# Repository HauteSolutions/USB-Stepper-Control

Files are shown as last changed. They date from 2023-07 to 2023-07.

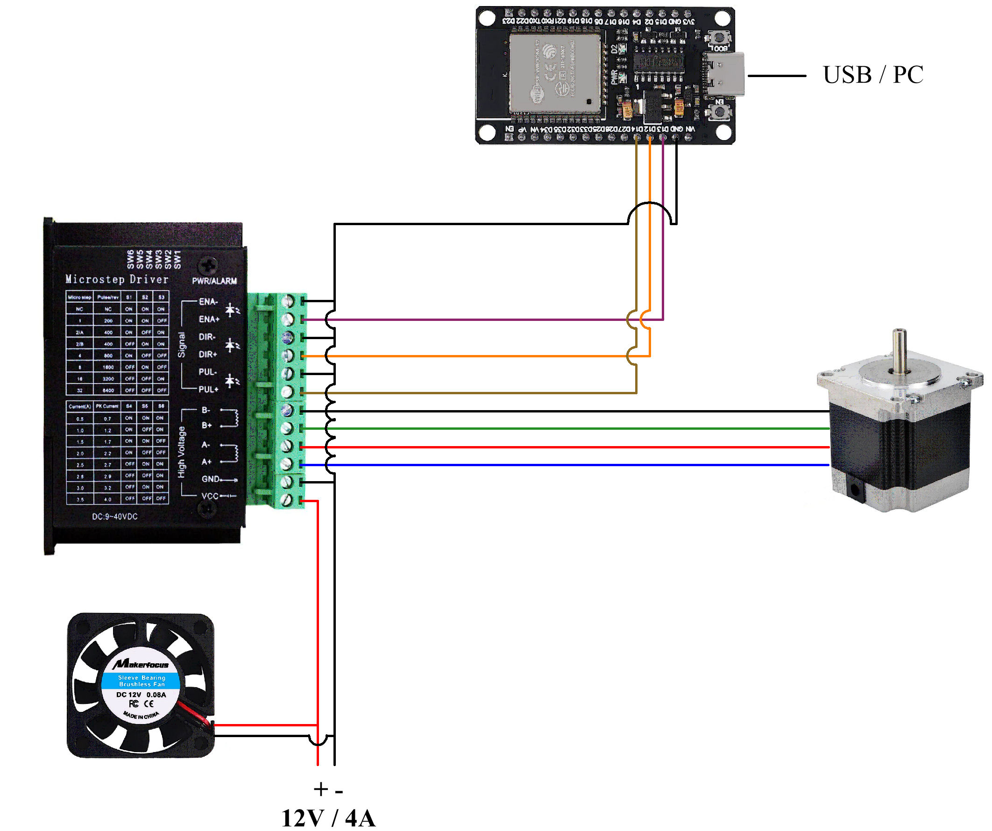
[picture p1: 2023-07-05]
Controller_Schematic.jpg

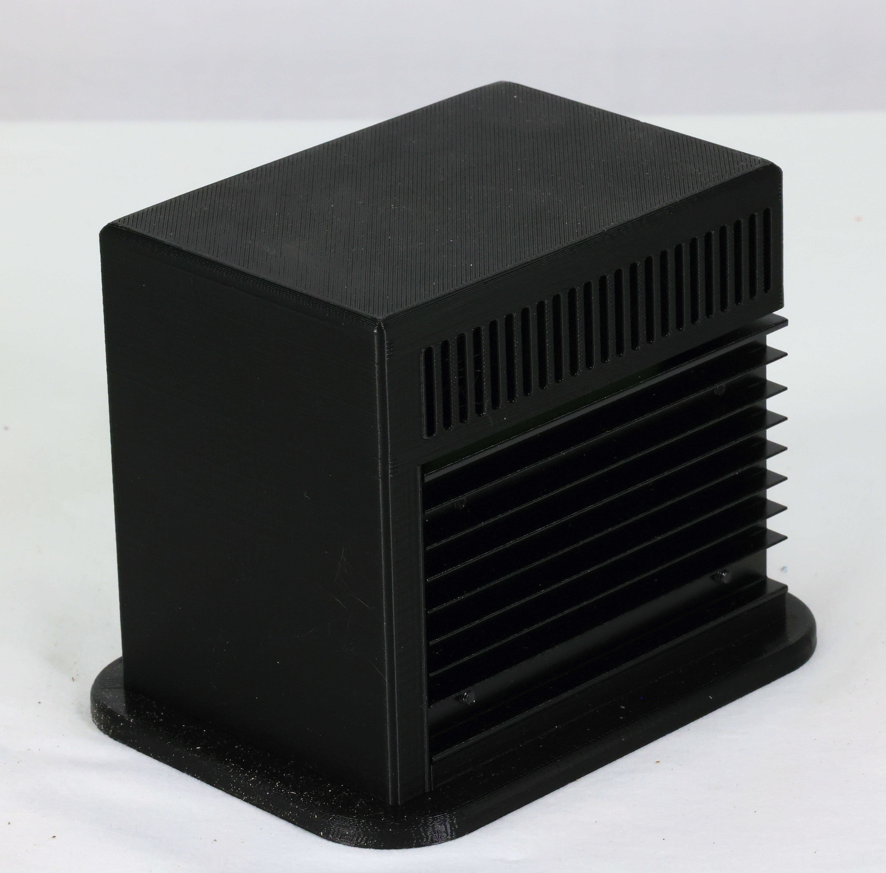
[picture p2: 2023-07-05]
photos/Controller Front.jpg

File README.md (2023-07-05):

# USB-Stepper-Control (and Rotary Pen Table Project)

A set of tools to provide simple control of a stepper from a PC USB Interface (Bridge: PC USB to AccelStepper Arduino Library)

The USB Stepper Control project provides direct control of stepper motors via a USB Connection to a PC.  This enables extended functionality for devices to be controlled via user interfaces or events directly from a Windows PC.  This project also includes the necessary 3D print files, parts list, and wiring diagrams to create a fully functional Rotary Pen Table for laser etching pens.  (The Rotary Table was the driving goal for this project!)

The Physical Connections are as follows:

     PC USB Serial Connection -> Microcontroller (ESP32, Arduino, etc) -> Stepper Driver -> Stepper Motor

The Logical Functionality is as follows:

     PC Interface (AutoIT) -> Microcontroller Control Software (ESP32, Arduino, etc) -> AccelStepper Arduino Library

There are two parts to this project:

1.  Microcontoller Side:  The microcontroller side utilizes the popular "AccelStepper" library to control a stepper driver/motor.  The AccelStepper library functions are effectively abstracted over a USB Serial interface.  A serial handshaking protocol is used to pass commands to the microcontroller (Arduino, ESP32, etc).  Both blocking and non-blocking functions are supported.  Basically, all "AccelStepper" functions are implemented and supported by passing serial commands directly over the usb interface with the appropriate number of parameters.  The Microcontroller side is simply used to objectify the library and once uploaded, very little ongoing maintenance should be required in order to maintain the microcontroller side as projects are added or updated on the PC Side.  (IOW: Functional logic can be entirely implemented/maintained on the PC side)  The microcontroller side should be largely static unless changes are required to support additional updates to the AccelStepper Library.

* Note that the Microcontroller (Arduino/ESP32) Side requires the AccelStepper Library: https://www.airspayce.com/mikem/arduino/AccelStepper/

2.  PC Side: The PC side exposes the "AccelStepper" function calls over the USB Serial Interface.  The actual function call is implemented as the first field in the serial command with additional fields provided for each of the required function parameters.  This effectively allows AccelStepper library functions to be directly called from a PC Application.

* Note that the PC (Autoit Side) requires the "ComUDF" Function Library:  https://www.autoitscript.com/forum/topic/189190-serial-port-udf-com-port-udf/

Once the Microcontroller code (USBStepperCtl.ino)is compiled and uploaded (to Arduino, ESP32, etc) then the PC Side (AutoIT) can be used to control the associated stepper.  Example code is provided using the AutoIT development environment (free).  (AutoIT excels in the simplicity of user interface creation, scripts can be compiled into standalone executables, and the development environment is freely available). The following example code fully implements the command construction and handshaking as required to implement the associated protocol.

PC (AutoIT) Examples:

USBStepperCtl.au3:  This is a very simply script demonstrating three different ways to move a stepper between various positions.  The associated INI file (of the same name) can be used to configure the operation of the program.  The [Config] section is used to define the COM Port where the stepper controller is connected, which demo program is to be run (RunDemo=Demo1, Demo2, or Demo3).  It also supports the ability to specify/maintain specific configuration parameters within separate INI sections (RunConfig=).  "MinPulseWidth" is also supported which is reportedly required for TB6600 Stepper Drivers.  The USBStepperCtl example provides no user interface and will simply run until the process is manually terminated.

Indexer.au3:  Is a sample utility developed to drive a rotary "Pen Table" for engaving using a Galvo Laser.  The format of the INI file is much like that used for USBStepperCtl example (above).The "RunConfig" option is used to designate a section which defines the stepper driver configuration parameters.  The Indexer example user interface supports initial adjustment/alignment of the rotary table (Tweak), an indexing function, the ability to disable/enable the stepper motor (for manual rotation or power savings), and a QUIT function.  Additionally, The Indexer utility (once compiled) can be called directly from the command line to control the rotary table using the command line parameters of "CW" (clockwise) or "CCW" (counter-clockwise) for rotation.  For example: Launch INDEXER.EXE, manually rotate the pen table to the desired position, "Enable" the stepper motor to grab the position, and then "Tweak" the rotation if needed to further adjust the position.  Then just call "Indexer CCW" or "Indexer CW" from your application as needed to precisely rotate the table

Through examination of both examples, it should be quite easy to duplicate the necessary code to implement a PC side control application as desired for a wide variety of applications.  

*** We have asked the developers at Lightburn to provide a "Before Job" and "After Job" command line option such that "Indexer" can be to control a virtually unlimited array of user developed solutions.

>--------------------------------------------------------------------------------

Rotary Pen Table Project:

This project consists of the following components:

- 3D Print File (STL) to create the Pen Wheel (in 4 quadrants): Pen_Wheel_Quarter.stl
- Acrylic Cut File (DXF) to create the foundation to which the Pen Wheel Quadrants are mounted: Pen_Wheel_Foundation.dxf
- 3D Print Files (STL) to create the Enclosure which holds the print wheel and ALL its components (Stepper, Driver, ESP32 Controller, Cooling Fan): Combined_Enclosure_Bottom.stl, Combined_Enclosure_Top.stl

...and if you would like to "split" the stepper motor from the control unit, here is another set of files.  The stepper "control" housing can then be used with ANY stepper (i.e. Rotary Chuck) which uses a standard 4-connector GX-16 aviation connector:

- 3D Print Files (STL) to create an Enclosure for JUST the controller components (without Stepper): Control_Enclosure_Bottom.stl, Control_Enclosure_Top.stl
- 3D Print Files (STL) to create an Enclosure for JUST the stepper iteself (without Driver, ESP32, or Cooling Fan): Stepper_Enclosure_Bottom.stl, Stepper_Enclosure_Top.stl

Parts List (about $65)

- ESP32 ($6): https://www.amazon.com/gp/product/B09GK74F7N
- Nema23 Stepper ($26):  https://www.amazon.com/dp/B00PNEPF5I
- TB6600 Driver ($10): https://www.amazon.com/dp/B07PQ5KNKR
- 12v 4A Power Supply ($13): https://www.amazon.com/dp/B07H493GHX
- Power Jack ($2): https://www.amazon.com/dp/B08SJM2G52
- 6.35mm Flange Coupling ($2): https://www.amazon.com/dp/B08334YZ9V
- 40mm 12v Fan ($3): https://www.amazon.com/dp/B07CH6YC32
- Fan Cover ($2): https://www.amazon.com/dp/B00E1LAWHA
- (For "split" housing) GX-16 Stepper Connector ($2): https://www.amazon.com/gp/product/B07D3DC1PD

A wiring Schematic for the "combined" enclosure is provided: Controller_Schematic.jpg

Photos of the various components (combined and seperate) are also provided

Project Notes

- An ESP32 microcontroller is used because of its small size, inexpensive cost, and powerful architecture.
- A TB6600 Stepper Driver is used as it is relatively inexpensive and provides very good control of our Nema23 stepper
- A 4A 12V power supply is used to provide higher power (4A) to maximize control (microstepping) and holding power of the stepper
- A fan, and colling vents in the enclosure, is used to maintain temps while operating

Assembly Notes

- Lightly coating the "holding slots" of the fully assembled pen wheel wiuth PlastiDip (or similar) will help minimize pen movement during rotation.  A small paint brush can be used to coat the slots to provide a very thin, rubberized, non-slip surface.

- An Adhesive Neoprene Pad cut to fit the bottom of the enclosure will help keep the device in place during operation

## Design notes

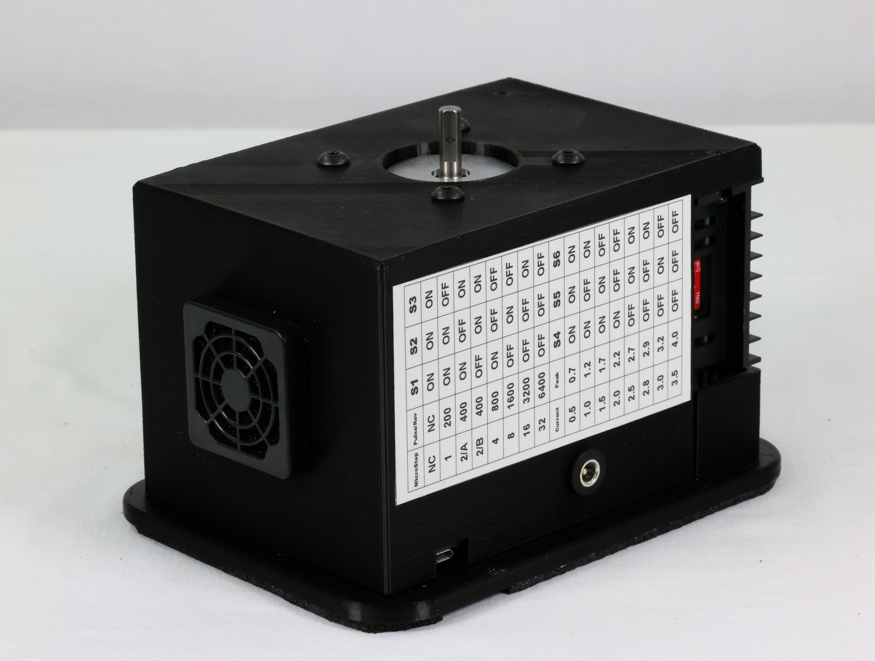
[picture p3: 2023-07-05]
photos/Integrated Rear.jpg

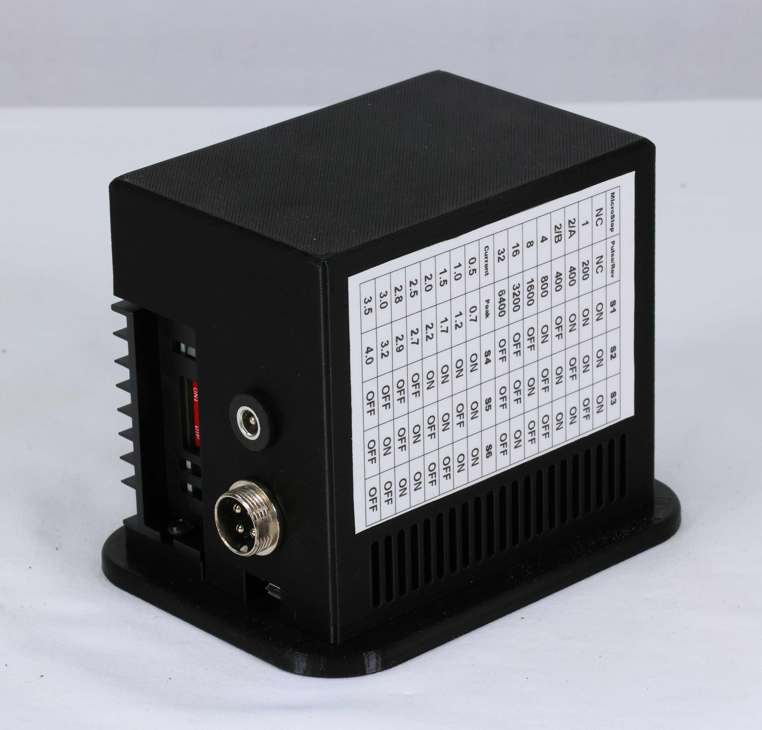
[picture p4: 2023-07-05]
photos/Controller Rear.jpg

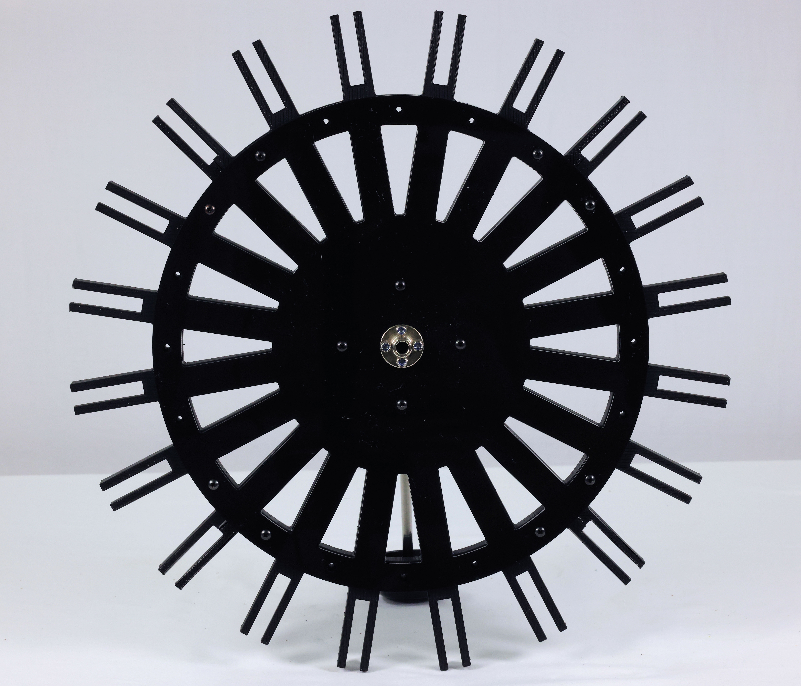
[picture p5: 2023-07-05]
photos/Wheel Bottom.jpg

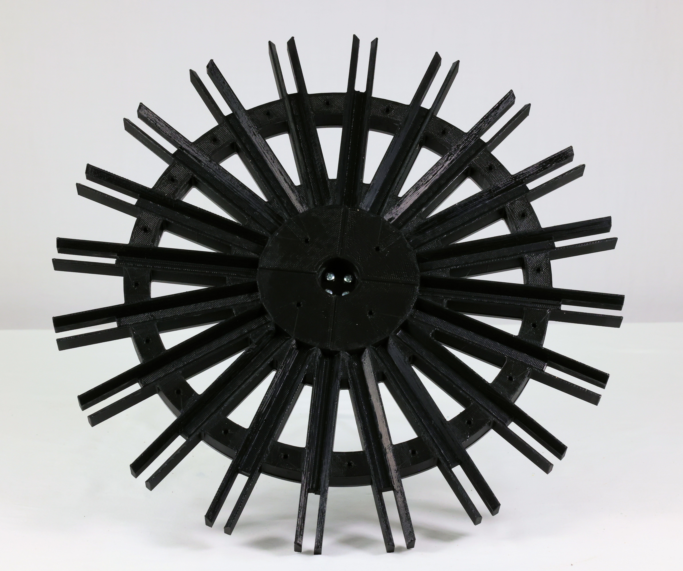
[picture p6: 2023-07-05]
photos/Wheel Top.jpg

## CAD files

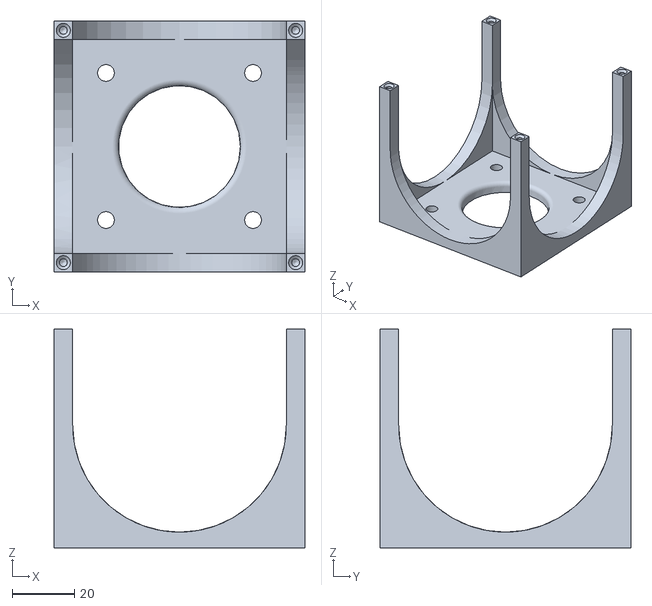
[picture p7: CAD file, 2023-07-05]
3D Print Files/Stepper_Enclosure_Top.stl
80.4 x 80.4 x 70.0

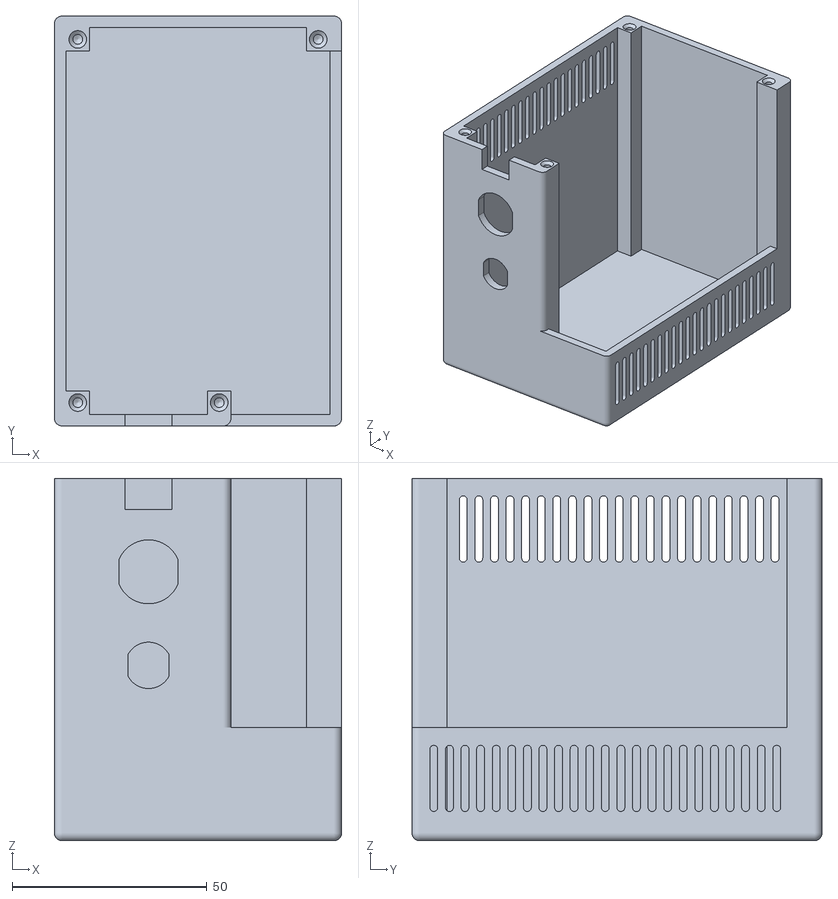
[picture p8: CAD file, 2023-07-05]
3D Print Files/Control_Enclosure_Top.stl
73.7 x 105.2 x 93.0

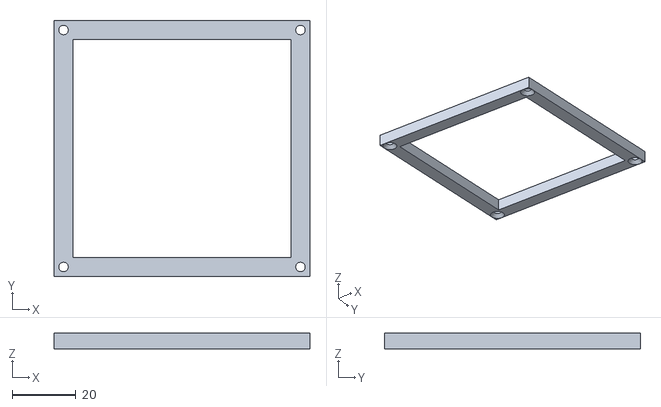
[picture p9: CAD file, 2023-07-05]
3D Print Files/Stepper_Enclosure_Bottom.stl
80.4 x 80.4 x 5.00

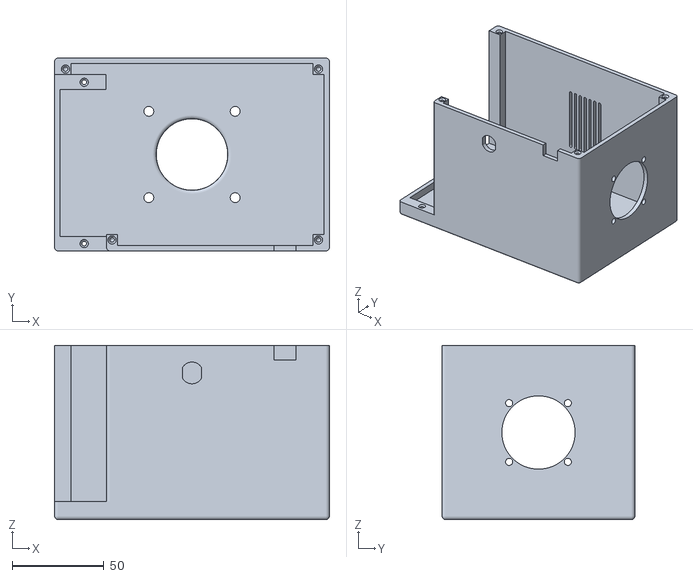
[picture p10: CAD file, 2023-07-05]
3D Print Files/Combined_Enclosure_Top.stl
150.0 x 105.2 x 95.0

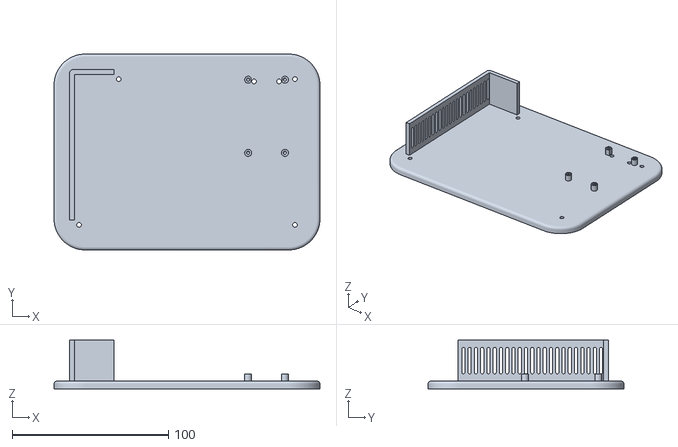
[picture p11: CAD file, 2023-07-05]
3D Print Files/Combined_Enclosure_Bottom.stl
170.0 x 125.2 x 31.0

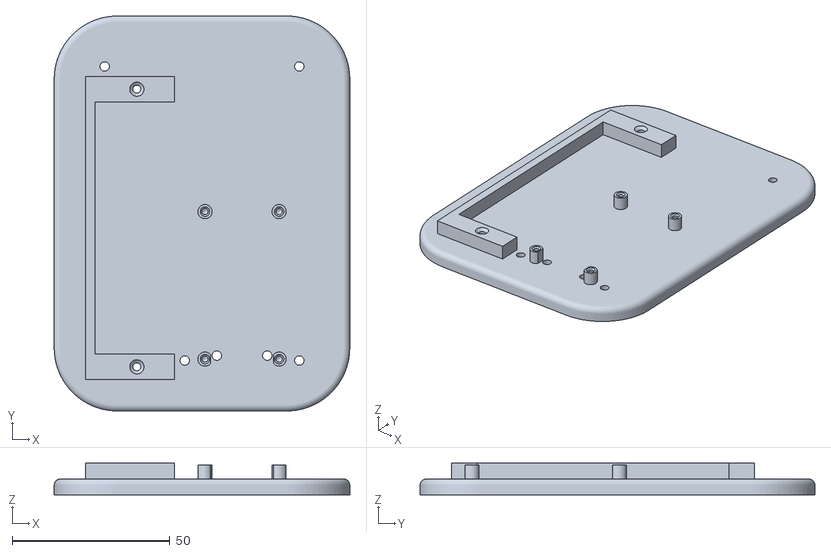
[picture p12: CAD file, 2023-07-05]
3D Print Files/Control_Enclosure_Bottom.stl
93.7 x 125.2 x 10.0

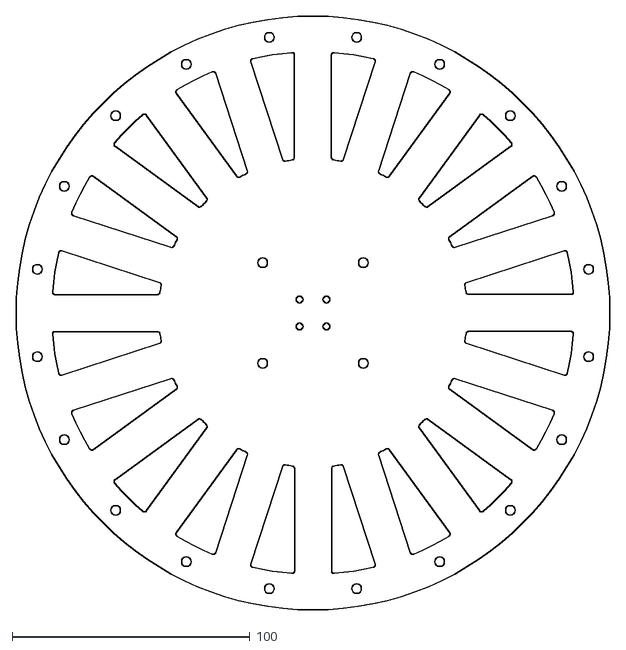
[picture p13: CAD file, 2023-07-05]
3D Print Files/Pen_Wheel_Foundation.dxf
250.0 x 250.0

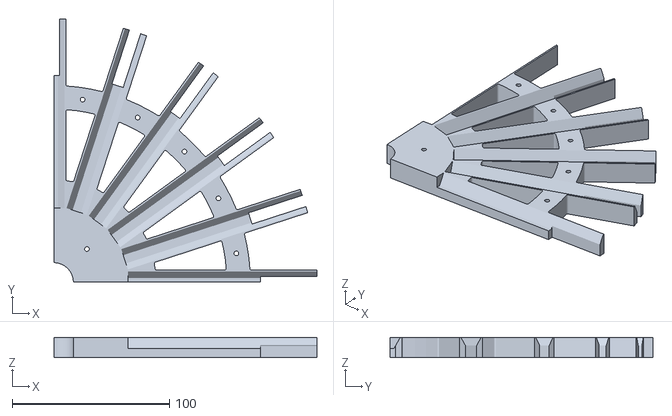
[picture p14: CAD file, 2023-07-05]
3D Print Files/Pen_Wheel_Quarter.stl
167.1 x 167.1 x 13.0

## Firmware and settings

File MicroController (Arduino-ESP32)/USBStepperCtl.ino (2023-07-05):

#include <AccelStepper.h>

#define DIR_PIN 12
#define STEP_PIN 14
#define ENABLE_PIN 13

char *CmdArray[] = {
  "setMinPulseWidth", 
  "setMaxSpeed",
  "setAcceleration",
  "setPinsInverted",
  "enableOutputs",
  "disableOutputs",
  "setEnablePin",
  "setSpeed",
  "setCurrentPosition",
  "stop",
  "maxSpeed",
  "speed",
  "targetPosition",
  "currentPosition",
  "distanceToGo",
  "isRunning",
  "move",
  "moveTo",
  "runToNewPosition",
  "runToPosition"
};
int NumCmds;

#define BUFFSIZE 512
char TxBuff[BUFFSIZE];
char RxBuff[BUFFSIZE];

char EOR = 0x09;  // End of Record = TAB
char EOM = 0x0A;  // Eond of Message = LF

int Position = 0;

AccelStepper stepper(AccelStepper::DRIVER, STEP_PIN, DIR_PIN);

void setup() {

  Serial.begin(9600);
  while (!Serial);
	
  RxBuff[0]='\0';
  TxBuff[0]='\0';

  NumCmds = sizeof(CmdArray) / sizeof(CmdArray[0]);

  stepper.setEnablePin(ENABLE_PIN);
  stepper.setPinsInverted(false, false, true);

  stepper.disableOutputs();
}

void loop() {
    if(CheckSerial(RxBuff, BUFFSIZE)) ProcessSerial(RxBuff);

    stepper.run();
}

int CheckSerial(char *buff, int buffmax) {
int c;
int i;

  while (Serial.available()) {
    c = Serial.read();
    i = strlen(buff); 
    if (i < (buffmax - 1)) {
      buff[i] = c;  
      buff[i+1] = '\0';
    }
    if (c == EOM) return strlen(buff);
  }

  return 0;
}

void ProcessSerial(char *Buff) {
long int PLong;

  PLong = GetLongParam(Buff, 1);
  strcpy(TxBuff, "OK");
  switch (GetCommandID(Buff, CmdArray, NumCmds)) {

    case 1:     // setMinPulseWidth
      stepper.setMinPulseWidth(PLong);
      break;

    case 2:     // setMaxSpeed
      stepper.setMaxSpeed(PLong);
      break;

    case 3:     // setAcceleration
      stepper.setAcceleration(PLong);
      break;

    case 4:     // setPinsInverted
      SetPinsInvertedHandler(Buff);
      break;

    case 5:     // enableOutputs
      stepper.enableOutputs();
      break;

    case 6:     // disableOutputs
      stepper.disableOutputs();
      break;

    case 7:     // setEnablePin
      stepper.setEnablePin(PLong);
      break;

    case 8:     // setSpeed
      stepper.setSpeed(PLong);
      break;

    case 9:     // setCurrentPosition
      stepper.setCurrentPosition(PLong);
      break;

    case 10:     // stop
      stepper.stop();
      break;

    case 11:     // maxSpeed
      dtostrf(stepper.maxSpeed(),1,2,TxBuff);
      break;

    case 12:     // speed
      dtostrf(stepper.speed(),1,2,TxBuff);
      break;

    case 13:     // targetPosition
      sprintf(TxBuff, "%ld", stepper.targetPosition());
      break;

    case 14:     // currentPosition
      sprintf(TxBuff, "%ld", stepper.currentPosition());
      break;

    case 15:     // distanceToGo
      sprintf(TxBuff, "%ld", stepper.distanceToGo());
      break;

    case 16:     // isRunning
      sprintf(TxBuff, "%s", stepper.isRunning() ? "true" : "false");
      break;

    case 17:     // move
      stepper.move(PLong);
      break;

    case 18:     // moveTo
      stepper.moveTo(PLong);
      break;

    case 19:    // runToNewPosition
      stepper.runToNewPosition(PLong);
      break;

    case 20:    // runToPosition
      stepper.runToPosition();
      break;

    default:
      sprintf(TxBuff, "Error%c%d", EOR, 1);
  }

  SendMessage(TxBuff);

  Buff[0] = '\0';
  return;
}

void SetPinsInvertedHandler(char *CmdBuff) {
int NumParams;
char Param[5][10];

  NumParams = CountDelims(CmdBuff, EOR);
  if(NumParams > 5) NumParams=0;
  
  for(int i=0; i<NumParams; i++) StrGetSlice(CmdBuff, EOR, i+1, Param[i], 10);

  switch (NumParams) {
    case 0:
      stepper.setPinsInverted();
      break;
    case 1:
      stepper.setPinsInverted(Param[1]);
      break;
    case 2:
      stepper.setPinsInverted(Param[1],Param[2]);
      break;
    case 3:
      stepper.setPinsInverted(Param[1],Param[2],Param[3]);
      break;
    case 5:
      stepper.setPinsInverted(Param[1],Param[2],Param[3],Param[4],Param[5]);
      break;
  }
}

void SendMessage(char *msg) {
  Serial.print(msg);
  Serial.write(EOM);
  Serial.flush();
}

long int GetLongParam(char *Buffer, int PNo) {
char Param[80];

  if(StrGetSlice(Buffer, EOR, PNo, Param, 80) == 0) return 0;
  return atol(Param);
}

int GetCommandID(char *astring, char *Array[], int NumCmds) {
int i;

  for (i=0; i<NumCmds; i++) {
    if(!strncasecmp(astring,Array[i],strlen(Array[i]))) return i+1;
  }
  return 0;
}

int CountDelims(char *astring, char delim) {
int i;
int len;
int count = 0;

  len = strlen(astring);
  for(i=0; i++; i<len) if(astring[i] == delim) count++;
  return count;
}

int StrGetSlice(char *Source, char Delim, int Pos, char *Slice, int MaxLen) {
int i;
int Len;
int SafeLen;
char *pStart;
char *pEnd;

  i = 0;
  pStart = Source;
  while (true) {
    pEnd=strchr(pStart, Delim);
    if(pEnd == NULL) {
      if(i < Pos) {
        if (Slice != NULL) strcpy(Slice, "");
        return 0;
      }
      pEnd=pStart+strlen(pStart);
    }
    
    if(i == Pos) {
      Len = (pEnd-pStart);
      if((Slice == NULL)  || (MaxLen == 0)) return Len;

      if(Len + 1 > MaxLen) SafeLen = MaxLen-1;
      else SafeLen=Len;

      strncpy(Slice, pStart, SafeLen);
      Slice[SafeLen] = '\0';
      return Len;
    }

    pStart = pEnd + 1;
    i++;
  }

  return 0;
}

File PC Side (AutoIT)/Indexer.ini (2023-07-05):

[Config]
ComPort=COM4
MinPulseWidth=20
RunConfig=1600SPR

[200SPR]
StepsPerRev=200
MaxSpeed=50
Acceleration=200
Speed=50
IndexDegrees=18

[400SPR]
StepsPerRev=400
MaxSpeed=100
Acceleration=400
Speed=100
IndexDegrees=18

[800SPR]
StepsPerRev=800
MaxSpeed=400
Acceleration=800
Speed=400
IndexDegrees=18

[1600SPR]
StepsPerRev=1600
MaxSpeed=400
Acceleration=1600
Speed=400
IndexDegrees=18

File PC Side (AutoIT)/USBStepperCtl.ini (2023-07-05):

[Config]
ComPort=COM3
MinPulseWidth=20
RunConfig=Default
RunDemo=Demo3

[Default]
StepsPerRev=1600
MaxSpeed=1000
Acceleration=200
Speed=500
